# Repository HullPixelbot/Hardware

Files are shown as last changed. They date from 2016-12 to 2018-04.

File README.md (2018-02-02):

# Hardware

This folder contains the design files for the 3D printed components along with the build instructions and the parts inventory for the HullPixelbot.

The stl folder contains folders for the 3D printed parts for the different robot elements. 

The HullPixelbot.dxf file contains the layouts for a laser cut chassis. The layers are identified with the suggested perspex thickness and the persex folder in the stl folder contains the extra elements (wheel hubs, bumpers, washers) that are not  presently laser cut. 

The HullPixelbot Connections file shows how the components are connected. This is explained in more detail in the learning part of this site. 

The parts list file holds a list of parts. (the clue is in the name)

Rob Miles

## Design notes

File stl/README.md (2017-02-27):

# 3D Printing Files

This folder contains all the files to print a HullPixelbot and accessories. You don't need to print them all to make a robot. Here are the ones that you need. 

## chassis - Basic HullPixelbot chassis

The basic HullPixelbot chassis just holds the motors, batteries and processor. You can start with this and then add the pixel and other items later. 

- base: this is the base of the HullPixelbot. You attach the motor supports, the stepper driver boards and the skid to the base. You need to print one of these.  The base can be fitted either way up. One way it has mounting pillars for an Arduino Uno or compatible, the other way up you can stick a breadboard on the top of the robot. 

- top: this is the top of the HullPixelbot. It holds the processor. You'll need to print one of these. 

- motorTowerLeft and motorTowerRight: these provide the sides of the robot. You attach the motor to a tower, which is then bolted to the base. 

- wheelLeft and wheelRight: these are the wheels for the robot. The wheels fit onto the shafts of the stepper motors and can be further secured with a bolt. 

- skidFront and skidBack: this is the skid that goes underneath the robot base. You can fit a 10mm ball bearing (or catapult ammunition) into the skid to provide a bearing surface for when the robot moves. You'll need to print two of these.

## ringLed - Pixel ring Display

The pixel display is a holder for a pixel ring that is mounted on top of the robot. There are two supports for the pixel, a cross piece that holds the pixel ring and a shade which fits over the top.

- ledSupportLeft and ledSupportRight: these are mounted on the base plate (using the bolts that secure the base plate to the motor towers. Each  contains a small square hole into which the cross-support piece fits. They also serve as a handles you can use to pick the robot up.

- ringCrossSupport: this is mounted between the handle support elements and holds a ring of Neopixel devices. The square pegs at each end of the cross support enage with the holes in the handle support.

- ringShade: this is the shade for the pixel ring. It can be printed using clear or white filament and will serve as a diffuser for the lights. It is a push fit onto the ringCrossSupport. Use your printer settings to print a single layer for best results.

- ledPipeShade: this is an alternative shade for the pixel ring. It contains a "light pipe" for each of the 12 leds in the ring. This can be used to get a different visual effect for the robot pixel, and also to make it easier for optical tracking of individual led elements in the single large pixel. 

## singleLed - single pixel display

This provides mountings for a single pixel that is mounted above the robot. It contains the same 
- ledCrossSupport: this is an alternative to the ring version which only holds a single pixel. 

- shade: this is a shade for a single pixel. It is a push fit onto the single pixel shade base.

- shadeBase: this holds the design for base that can hold a single Neopixel and be bolted to the rear of the robot base.

## Distance Sensor

You can fit a distance sensor on the front of your robot. The sensor also has fittings for three lignt sensors. It bolts into holds on the base of the robot. It is in the file distanceSensorHolder

## Power Switch Holder

If you wish to add a rocker switch to turh the robot on and off you can use this holder to hold the switch, which can then be bolted to the back of the robot. It is in the file powerSwitchHolder.

## Breadboard shelf

If you have constructed your robot using an Arduino and want to add a second processor the breadboard shelf can be printed and mounted above the Arduino using the same bolt holes. You can then stick a small breadboard to the shelf and connect it to the Arduino underneath.

## Cheese Plate

If you want your robot to be able to carry cheese around you can print a cheese plate that fits around the large pixel ring and lets you move small pieces of cheese around.

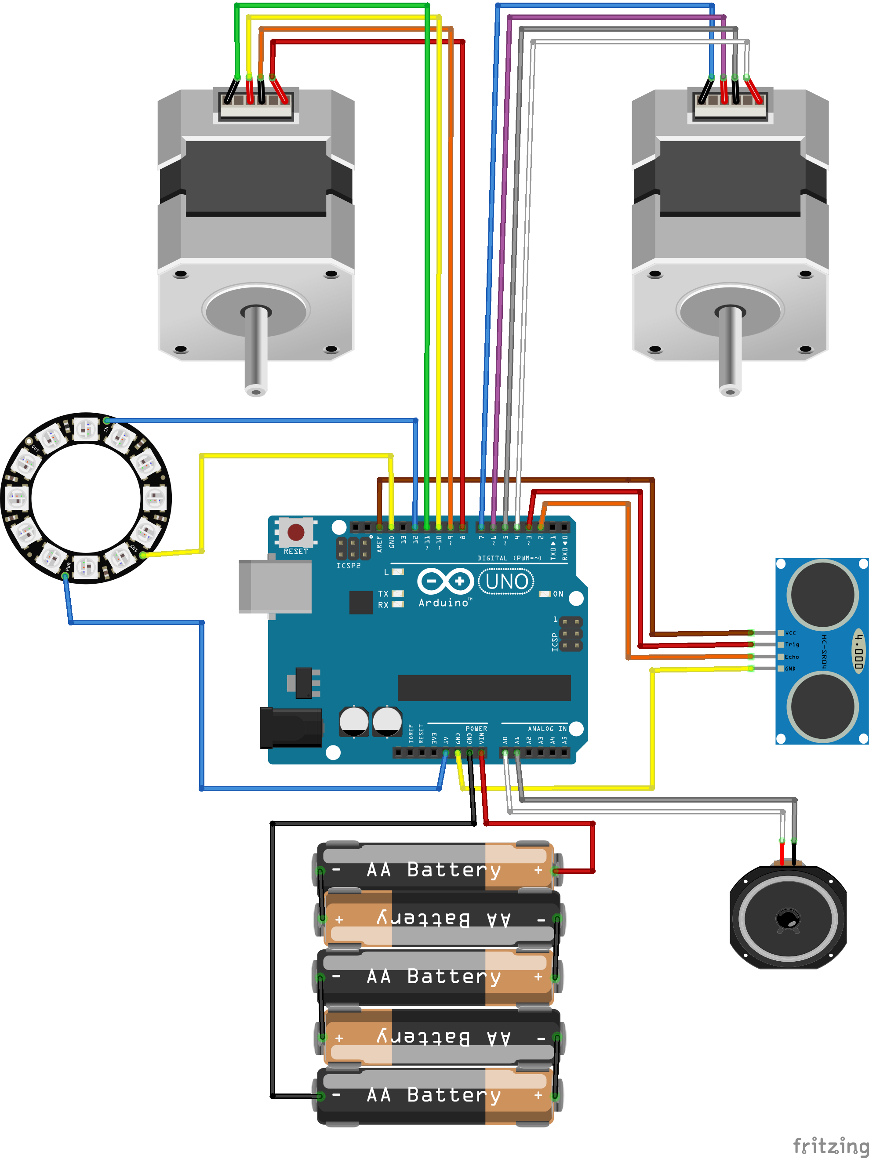
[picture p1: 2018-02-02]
Hullpixelbot Connections.png

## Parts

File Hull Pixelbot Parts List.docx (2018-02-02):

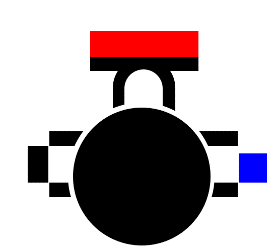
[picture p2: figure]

Hull Pixelbot Parts List

M3 6mm buttonhead bolt | 6
M3 10mm buttonhead bolt | 26
M3 16mm buttonhead bolt | 0
M3 10mm countersunk bolt | 2
M3 nut | 24
Robot Top | 1
Robot Base | 1
Robot wheel hub | 2
Robot Wheel | 2
Robot Bumper | 2
Robot Side | 2
Spacer washers | 8
Power switch holder | 1
Stepper Driver Board | 2
Stepper Motor | 2
Cable MM 20cm black | 1
Cable MM 20cm red | 1
Cable FF 20cm black | 1
Cable FF 20cm red | 1
Cable MF 20cm green,yellow, orange,red | 1
Cable MF 20cm white, grey, purple, blue | 1
Cable MF 20cm yellow, orange, red, brown | 1
Rocker switch | 1
Arduino Uno | 1
Battery holder | 1
AA Batteries | 5
HC-SR04 Distance sensor | 1

Version 1.0 Feb. 2018
Rob Miles

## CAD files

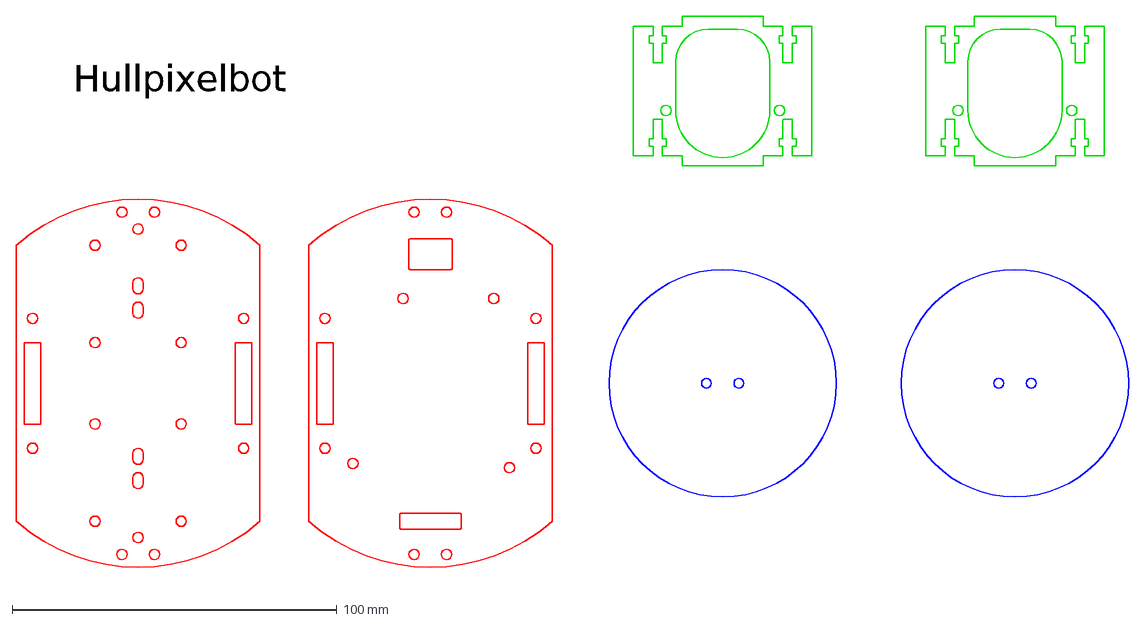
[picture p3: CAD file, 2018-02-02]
HulPixelbot.dxf
Hullpixelbot

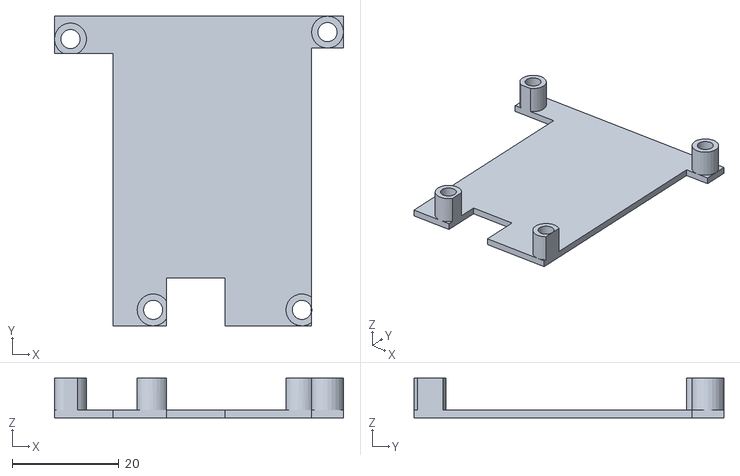
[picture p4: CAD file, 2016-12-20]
stl/breadboard/breadboardShelf.stl
54.2 x 58.1 x 7.50

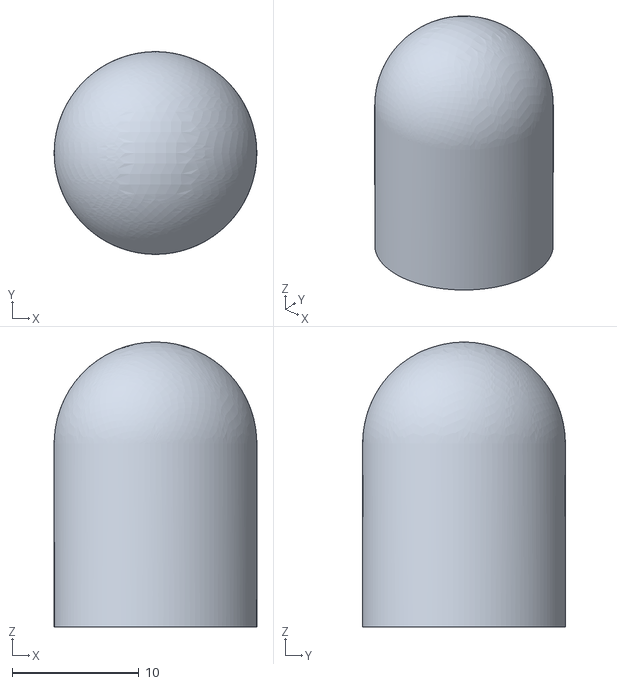
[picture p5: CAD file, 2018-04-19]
stl/chassis/solidSkidBack.stl
16.0 x 16.0 x 22.5

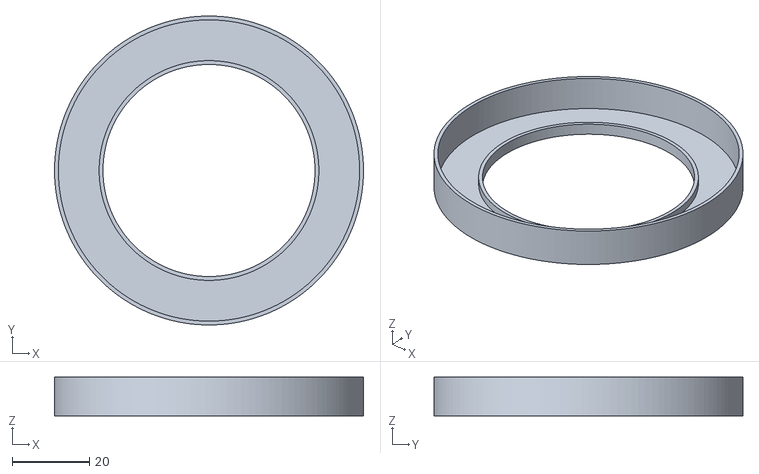
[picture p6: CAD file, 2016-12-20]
stl/cheese/cheesePlate.stl
80.0 x 80.0 x 10.0

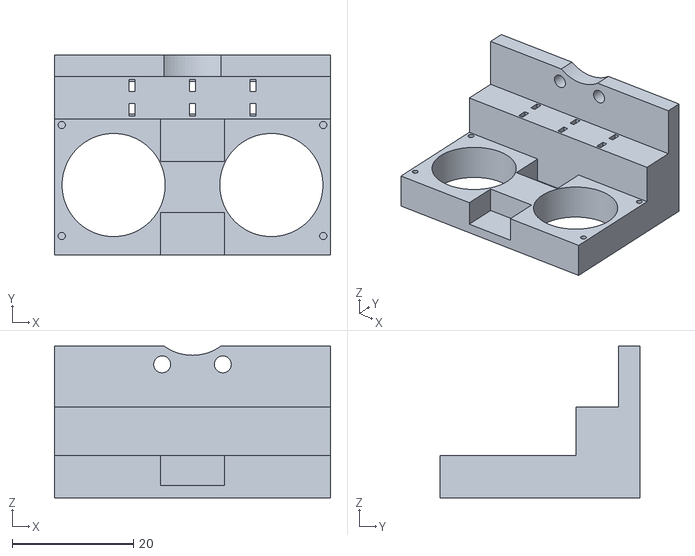
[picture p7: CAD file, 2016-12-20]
stl/distanceAndLightSensor/distanceSensorHolder.stl
45.5 x 32.9 x 25.0

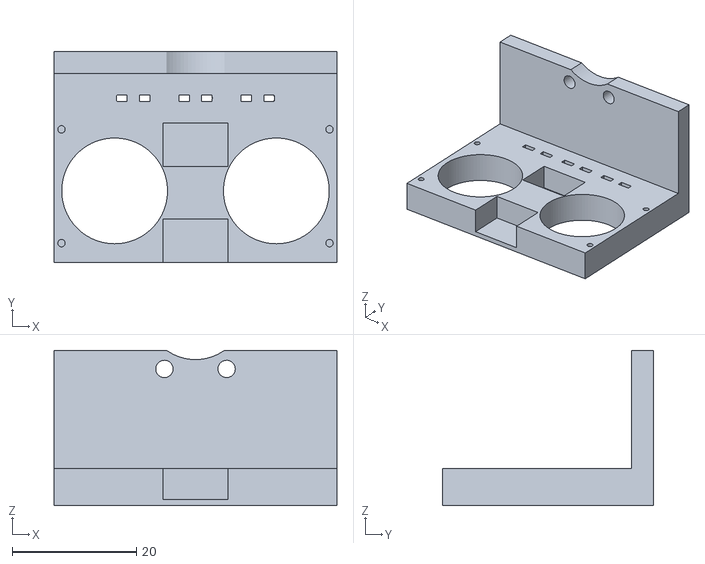
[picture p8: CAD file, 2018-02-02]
stl/perspex/distanceSensorHolder.stl
45.5 x 33.9 x 25.0

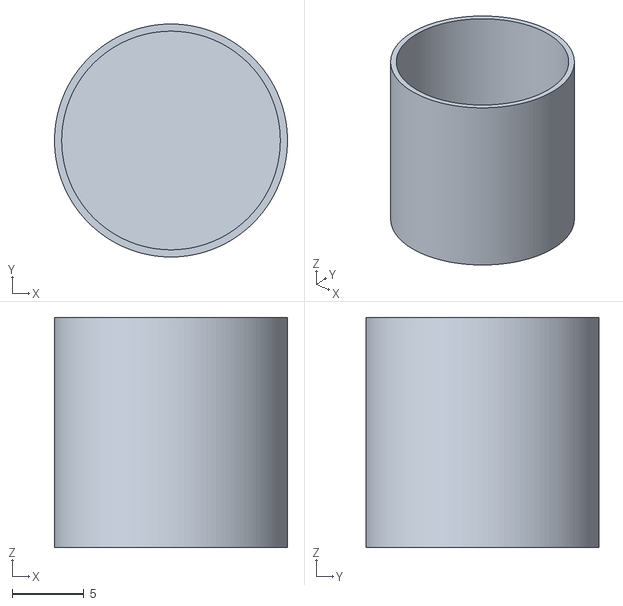
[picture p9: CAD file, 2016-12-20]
stl/rearLed/shade.stl
16.2 x 16.2 x 16.0

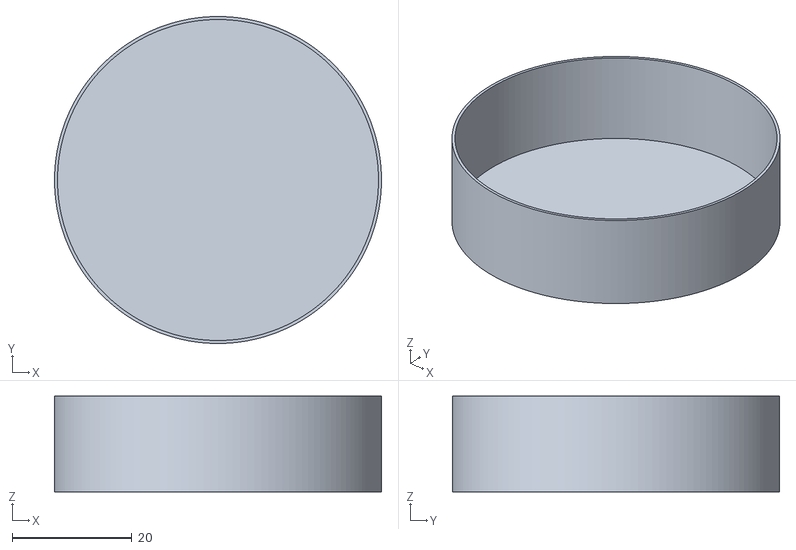
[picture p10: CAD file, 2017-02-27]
stl/ringLed/ringShade.stl
54.7 x 54.7 x 16.0

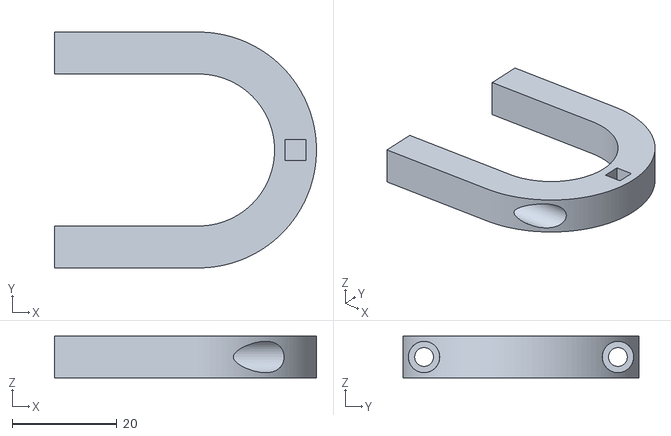
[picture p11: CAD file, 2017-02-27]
stl/singleLed/ledSupportRight.stl
50.0 x 45.0 x 8.00

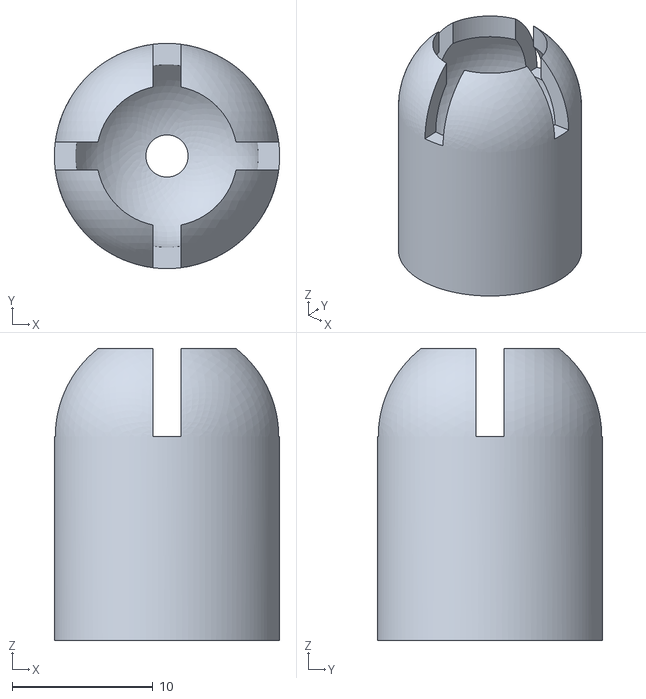
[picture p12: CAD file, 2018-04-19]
stl/chassis/skidFront.stl
16.0 x 16.0 x 20.7

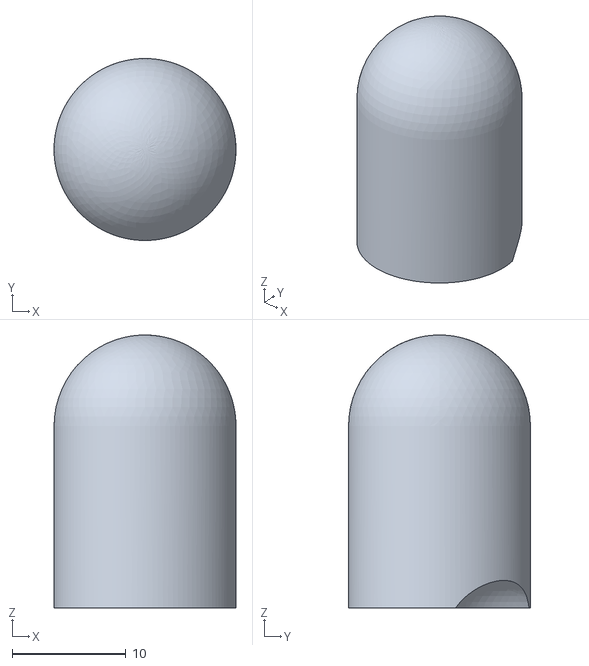
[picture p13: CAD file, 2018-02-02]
stl/perspex/skidFront.stl
16.0 x 16.0 x 24.0

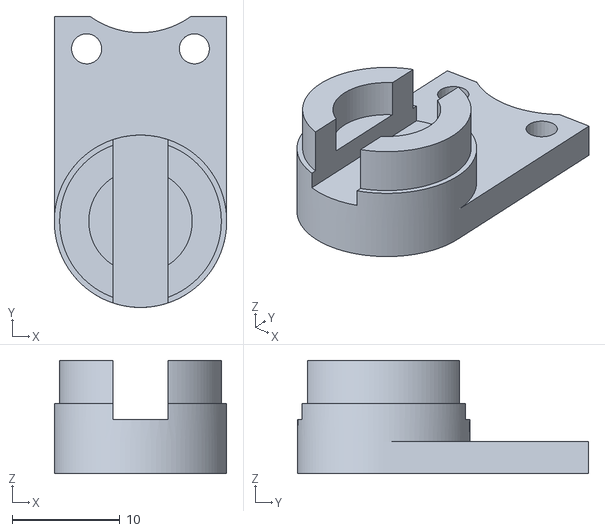
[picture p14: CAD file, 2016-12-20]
stl/rearLed/shadeBase.stl
16.0 x 27.0 x 10.5

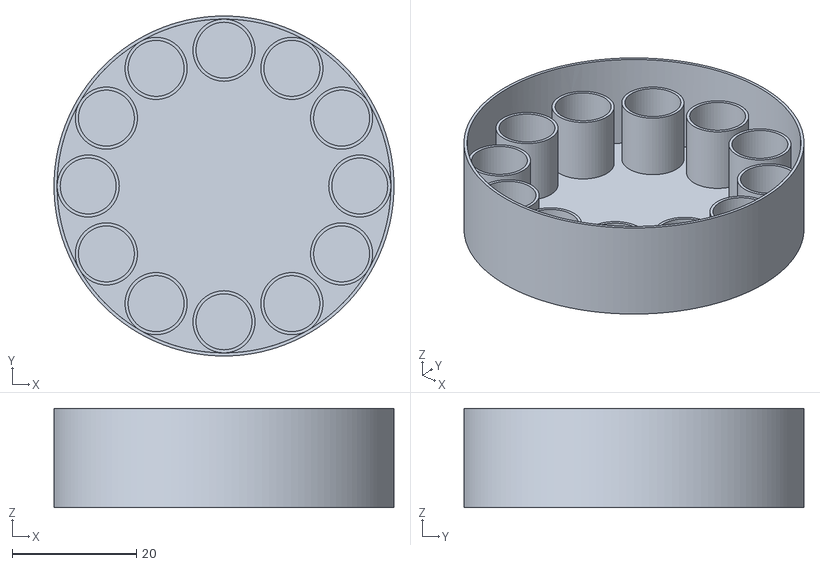
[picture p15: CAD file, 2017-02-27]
stl/ringLed/ledPipeShade.stl
54.7 x 54.7 x 16.0

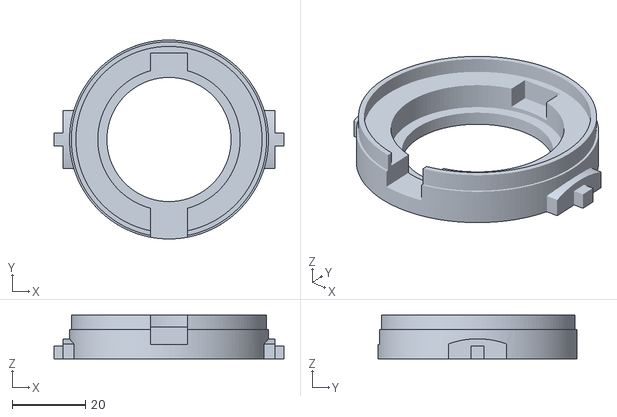
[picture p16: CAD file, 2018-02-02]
stl/perspex/ringCrossSupport.stl
63.0 x 54.5 x 12.0

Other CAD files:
stl/singleLed/shade.stl
stl/chassis/skidBack.stl
stl/ringLed/ledCrossSupport.stl
stl/singleLed/ledSupportLeft.stl
stl/chassis/alloyWheel.stl
stl/chassis/base.stl
stl/chassis/motorTowerLeft.stl
stl/chassis/motorTowerRight.stl
stl/chassis/solidSkidFront.stl
stl/chassis/top.stl
stl/chassis/wheelLeft.stl
stl/chassis/wheelRight.stl
stl/perspex/handleSupport.stl
stl/perspex/lefthub.stl
stl/perspex/powerSwitchHolder.stl
stl/perspex/righthub.stl
stl/perspex/shadeBase.stl
stl/perspex/skidBack.stl
stl/perspex/washer.stl
stl/perspex/washers.stl
stl/perspex/wheelhub.stl
stl/ringLed/ledSupportLeft.stl
stl/ringLed/ledSupportRight.stl
stl/ringLed/ringCrossSupport.stl
stl/singleLed/ledCrossSupport.stl

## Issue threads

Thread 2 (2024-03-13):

Updates... Pico

bsimmo, 2024-03-13:
Are there any updates for the Pico setup, enhancements, etc..

BNNorman, 2024-03-13:
This is where it's at...

https://github.com/HullPixelbot/PICO-HullPixelbot

bsimmo, 2024-03-13:
This is the component checklist and stl/dxf section.  Not the code.

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

BNNorman, 2024-03-13:
??? The UF2  files are there to load onto a Pico
On 13/03/2024 13:30:31, Ben ***@***.***> wrote:
This is the component checklist and stl/dxf section. Not the code.

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

—
Reply to this email directly, view it on GitHub [https://github.com/HullPixelbot/Hardware/issues/2#issuecomment-1994411892], or unsubscribe [https://github.com/notifications/unsubscribe-auth/ADY5NXNMXBLXNJESMNMQ4MLYYBIHPAVCNFSM6AAAAABEUBUX3SVHI2DSMVQWIX3LMV43OSLTON2WKQ3PNVWWK3TUHMYTSOJUGQYTCOBZGI].
You are receiving this because you commented.Message ID: ***@***.***>
[0832f4ba-4721-4865-8913-163b26a4bee6]

bsimmo, 2024-03-13:
Yes over there in that repository, but the repository I am in here is not
that one. Here it is the physical stuff, the wheels the part list, the
body...
They are all at Uno 2018 standards.
Quote
These files contain construction details, stl files for 3d printing and dxf
files for laser cutting robots.

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

BNNorman, 2024-03-13:
Ok, the physical bot hasn't changed only the electronics.

I saw Rob this morning and , because Ross is bringing a bunch of UNO/Wemos devices, Rob is in two minds about building Pico bots or just using the Uno bots.

If you are still buying a bunch of Pico-W I will have two and I think Ross said he'd have one.
On 13/03/2024 13:53:08, Ben ***@***.***> wrote:
Yes over there in that repository, but the repository I am in here is not
that one. Here it is the physical stuff, the wheels the part list, the
body...
They are all at Uno 2018 standards.
Quote
These files contain construction details, stl files for 3d printing and dxf
files for laser cutting robots.

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

—
Reply to this email directly, view it on GitHub [https://github.com/HullPixelbot/Hardware/issues/2#issuecomment-1994460172], or unsubscribe [https://github.com/notifications/unsubscribe-auth/ADY5NXKSKBMGHF3M3S6V54DYYBK4JAVCNFSM6AAAAABEUBUX3SVHI2DSMVQWIX3LMV43OSLTON2WKQ3PNVWWK3TUHMYTSOJUGQ3DAMJXGI].
You are receiving this because you commented.Message ID: ***@***.***>
[827eab7d-5241-459e-8a8e-be628af1e35e]

bsimmo, 2024-03-13:
Really just an update to the list of parts in here, the pico set and the
ESP setup. No changes to the mountings?

And there is a pull request waiting I see, looks to be for different shaped
driver boards.

Brain transplant the Pico in? , but I think some seemed interested in the
actual build part of it.

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

BNNorman, 2024-03-13:
Ok, see you wed.
On 13/03/2024 15:16:25, Ben ***@***.***> wrote:
Really just an update to the list of parts in here, the pico set and the
ESP setup. No changes to the mountings?

And there is a pull request waiting I see, looks to be for different shaped
driver boards.

Brain transplant the Pico in? , but I think some seemed interested in the
actual build part of it.

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

—
Reply to this email directly, view it on GitHub [https://github.com/HullPixelbot/Hardware/issues/2#issuecomment-1994638656], or unsubscribe [https://github.com/notifications/unsubscribe-auth/ADY5NXJVBXYUBMNMC6YWIALYYBUUTAVCNFSM6AAAAABEUBUX3SVHI2DSMVQWIX3LMV43OSLTON2WKQ3PNVWWK3TUHMYTSOJUGYZTQNRVGY].
You are receiving this because you commented.Message ID: ***@***.***>
[d9257216-0829-41cb-a054-24395ebf0566]

CrazyRobMiles, 2024-03-14:
Sorry for the confusion folks. I need to pull the whole thing together a bit more. The plan for robots going forwards is to use PICOW plugged into a breadboard (I've got a bunch of them). The breadboard can be stuck straight onto the top plate of the robot (we flip the plate upside down if it is a 3D printed one with pillars for an Arduino). I'm going to bring some of my laser cut chassis components and some bits and bobs for next week if someone really wants to build from scratch.

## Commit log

2016-12-20 Initial Commit
    First versions of all the STL files for printing a HullPixelbot
    [base.stl, breadboardShelf.stl, cheesePlate.stl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]
2016-12-21 Created separate folder for stl files
    [base.stl, breadboardShelf.stl, cheesePlate.stl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]
2017-02-27 Partitioned the design into folders
    [alloyWheel.stl, base.stl, breadboardShelf.stl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]
2018-02-02 Perspex Files
    Now contains a dxf file for cutting a perspex robot and the stl files
    for the 3d printed elements to go with it.
    [HulPixelbot.dxf, alloyWheel.stl, base.stl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]
2018-04-19 Solid Skids
    Added some solid skids for the normal chassis.
    [skidBack.stl, skidFront.stl, solidSkidBack.stl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]
